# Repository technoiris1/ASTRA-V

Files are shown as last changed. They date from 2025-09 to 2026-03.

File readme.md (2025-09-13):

# ASTRA-V

heyo! Manan this side - this is my second big hardware project after my foldable 3d printer - ASTRA-V. Stands for Autonomous Stabilised Thrust Recovery Ascent Vehicle.<br>
CAD
CAD
The concept is simple - Go up - attain free fall - thrust again a lil when around 3 feet from the ground - land.

Its using LiDars to calculate the height precisely and they are pretty quick, so no problems.

First iteration -
This very iteration of ASTRA-V has the following tasks - going up 15 feet, attaining a proper stable freefall and then land. Now the word *land* is the main thing, so like this is what the hardest part is - so lets discuss the whole thing step by step.

## Launch
### Trigger
We are using a RF module to trigger the launch, it is in the flight controller.
### Process
The Servo motor will be kicked by the flight controller - which will open the flow of the O2 into the Acrylic Rod Chamber(We will come to the fuel part later on), and along with the servo - an arc ignitor will also be kicked which will burn the fuel. *sshhhhhhhhhhiiiiiiiiuuuuuuuuu* and with that the burnt fuel gases will come out pressurized of the nozzle and *shrrrooooommmm* the rockets up - it will go up 30 feet in this iteration.

## Free fall
Pretty simple, once reached the desired height(30 feet here) the valve will be kicked to close. Thus no oxidiser - thus no thrust and no more going up. Then it will just fall down - tearing down the vigilantly through the air.

## Landing
Now this is the special sauce, the complex thing - in simple words - LiDar sensors are highly sensitive sensors which mainly work on lasers so really quick. They will be sensing the altitude and sending it to the flight computer, now as soon as the altitude or around 15 feet (in this case) is reached - the computer will kick up the servo and ignitor once again to push enough thrust to neutralise the G force attained in the freefall. So like - the whole rocket will have a gentle touchdown in the air using thrusters. Now along with the engine mechanism, one more thing kicked would be the servo motors to deploy the landing legs - they have a really wide span as you can see in the images - so it gonna land really well.

## Flight Controller
Flight controller is a custom made from scratch which uses Pi pico as the main board. It uses MPU-6050 as the Gyro and BMP-280 as the altimeter as its a barometer. It has pins for breakouts of all these things along with connections with landing servos, LiDar sensors, Fuel Servos and the Arc Ignitor. It has 7 motor connections, 2 LiDar, 1 for MPU6050 and BMP280 each, it has different capacitors placed overall for fluctuations etc.
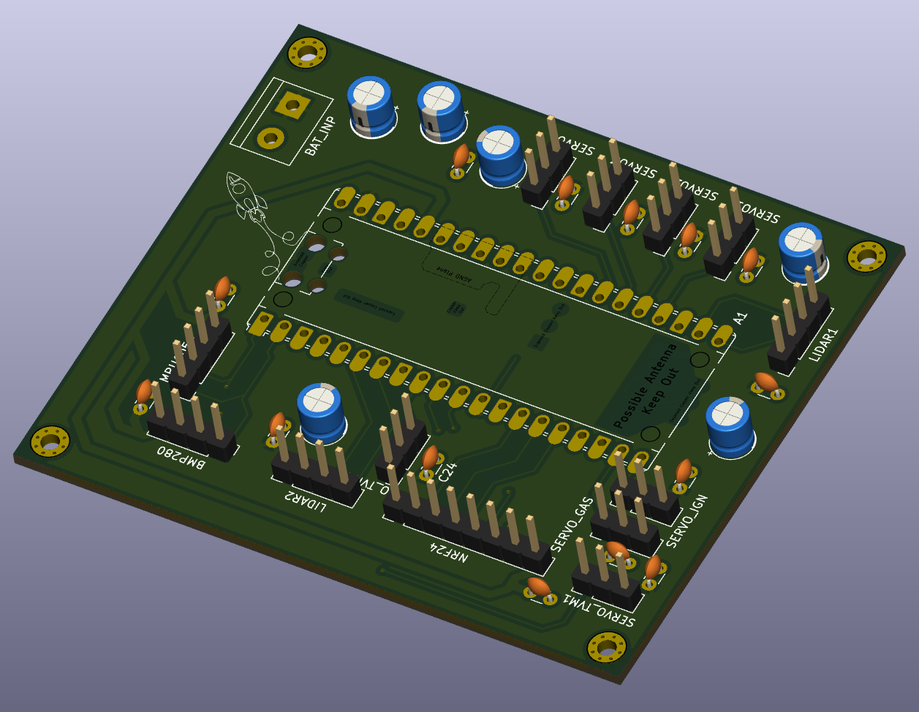
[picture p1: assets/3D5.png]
pcb


## Fuel
It is using Acrylic as a fuel along with O2 as the oxidiser. Pretty simple there is a chamber with acrylic rod and a servo controlled apparatus for the input of oxygen into the chamber. So the burnt O2 will heat up and burn the Acrylic rod, thus the Acrylic vapours will move out really really quickly off the nozzle providing thrust.

## Rocket motor and thrust vectoring
I am working on a basic servo controlled thrust vectoring system to control the direction of the thrust. This will allow for more precise control of the rocket's trajectory. The servos will be fitted on two different rings, one ring with a servo will be connected to the tube body of rocket and it will rotate another ring inside it, which is housing another servo and that servo will be connected to a ring joint to the rocket motor. So in this way there will be a whole 2-axis thrust vectoring system. I am currently working on the design and 3d model, will put here as soon as i'm done.

## Why am I making this thing?
cuz am crazy

## BOM
| ASTRA-V | 1 | 2 |  3 | 4 |  5 |  6 |
|:---|:---|:---|:---|:---|:---|:---|
| ASTRA | Autonomous Stabilised Thrust Recovery Ascent | | | | | |
| | | | | | | |
| BOM- | | | | | | |
| Name | Use case | price each | units | total price inr | total price usd | link |
| MG946R servo motors | Landing legs deployment | 800 | 4 | 3200 | 37 | https://thinkrobotics.com/products/standard-metal-servo-mg946r-1?variant=12765401514056 |
| LiDar sensor | to measure height quickly | 2500 | 2 | 5000 | 57 | https://thinkrobotics.com/products/tf-luna-lidar-tof-distance-ranging-sensor-8m |
| Raspberry pi pico W | the main controller of the flight | 700 | 2 | 1400 | 16 | https://thinkrobotics.com/products/raspberry-pi-pico-w-online?variant=44615124386109 |
| BMP280 breakout | the altimeter of the flight ctrl | 70 | 2 | 140 | 2 | https://thinkrobotics.com/products/bmp280-barometric-sensor-module-3-3v-5v?variant=32045116325974 |
| MPU 6050 | gyro sensor | 300 | 2 | 600 | 7 | https://thinkrobotics.com/products/mpu6050-gyroscope-sensor?variant=16158094786632 |
| nrf module | trigger for rocket to go boom | 80 | 2 | 160 | 2 | https://roboticsdna.in/product/nrflongrenge24l01/ |
| pin headers | pin headers on pcb | 11.5 | 20 | 250 | 3 | https://thinkrobotics.com/products/single-row-2-54-mm-pitch-header-40-pin?variant=12744266055752 |
| battery | battery | 1900 | 1 | 1900 | 22 | https://robocraze.com/products/bonka-2200mah-35c-3s1p-11-1v-lipo-battey?_pos=1&_sid=bea5fbb80&_ss=r |
| battery charger | battery charger | 350 | 1 | 350 | 4 | https://robocraze.com/products/b3-pro-li-po-battery-charger?_pos=2&_sid=bea5fbb80&_ss=r |
| 12v to 5v stepdown | as the name suggests, its the best i could find right now as i need >15A to feed to all the servos and lidars and all, gonna use a simpler one if found | 1300 | 1 | 1300 | 15 | https://www.amazon.in/Regulator-Converter-Step-Down-Waterproof-Transformer/dp/B0BB7TNNR9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 |
| 0.1uf ceramic cap | on pcb | 5 | 3 | 15 | 1 | https://quartzcomponents.com/products/10000-pf-0-1uf-ceramic-capacitor?_pos=1&_sid=c9f6e0456&_ss=r |
| 470uf cap | on pcb | 7 | 3 | 21 | 1 | https://quartzcomponents.com/products/470uf-50v-electrolytic-capacitor?_pos=1&_sid=1ae57eeec&_ss=r |
| 100uf cap | on pcb | 3 | 10 | 30 | 1 | https://quartzcomponents.com/products/100%CE%BCf-35v-radial-electrolytic-capacitor?_pos=3&_sid=f5c2847a1&_ss=r |
| 10uf cap | on pcb | 3 | 10 | 30 | 1 | https://quartzcomponents.com/products/10uf-50v-electrolytic-capacitor?_pos=2&_sid=5efdc15a5&_ss=r |
| push button | to be on the fire remote and some other usecases like replacing the arc ignitor small button with large ones to make it easier to work with | 20 | 3 | 60 | 1 | https://thinkrobotics.com/products/6mm-tactile-push-button-pack-of-20?variant=33484370313302 |
| arc igniter | lighter for the fuel etc. | 150 | 2 | 300 | 4 | https://quartzcomponents.com/products/arc-cigarette-lighter-parts-diy-electronic-lighter-kit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 |
| 18650 li-on battery | battery for the arc igniter | 100 | 2 | 200 | 3 | |
| 18650 battery charger | charger for the battery | 100 | 1 | 100 | 2 | https://quartzcomponents.com/products/18650-li-ion-battery-charger-for-single-cell?_pos=2&_sid=500a0bb39&_ss=r |
| 18650 battery holder  | holder for the battery | 25 | 1 | 25 | 1 | https://quartzcomponents.com/products/single-cell-18650-li-ion-battery-holder?_pos=1&_sid=1d517396f&_ss=r |
| flight controller PCB | main board | 5000 | 1 | 5000 | 57 | https://github.com/Manan-Coder/ASTRA-V/tree/main/Flight%20Controller |
| cardboard tube | for the main tube, it will be having the glass cloth on it | 675 | 1 | 675 | 8 | https://www.amazon.in/Inches-Mailing-Tubes-Metal-Length/dp/B0CPWVSQKS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 |
| fibre glass cloth | to make the main tube and make it durable | 650 | 1 | 650 | 8 | https://www.amazon.in/Fiber-Glass-Cloth-Thickness-10/dp/B0CX1W4TBQ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 |
| epoxy resin | to stick the glass cloth to the main tube | 500 | 1 | 500 | 6 | https://www.amazon.in/gp/product/B0F5W94NLF/ref=ewc_pr_img_1?th=1 |
| Carbon Fibre rods | Landing legs | 140 | 12 | 1680 | 20 | https://thinkrobotics.com/products/carbon-fiber-solid-tube-1-m?variant=39329659650134 |
| oxygen can | oxidiser for fuel | 1300 | 1 | 1300 | 15 | https://www.amazon.in/breathing-difficulties-Respiration-Lightweight-Travel-Friendly/dp/B0DNXRSX7V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 |
| acrylic rod | main fuel on which oxygen act as an oxidiser | 700 | 1 | 700 | 8 | https://www.amazon.in/Global-Plexiglass-Transparent-UV-Resistant-Diameter/dp/B07SR8LMRX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 |
| tube clamps | clamps for the tube carrying oxygen to the chamber | 160 | 1 | 160 | 2 | https://www.amazon.in/kitchenware-Store-clamp-pipe-safety/dp/B096NPHQLF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 |
| oxygen tube | the tube which will carry the oxygen to the chamber | 200 | 2 | 400 | 5 | https://www.amazon.in/ALEXERA-Mediplus-Oxygen-Tube-Length/dp/B0DDH3J4RS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 |
| aluminium tube | it will be the body of the rocket motor, the whole outer casing for safety and all that stuff | 1500 | 1 | 1500 | 18 | https://www.amazon.in/uxcell-Aluminum-Length-Seamless-Straight/dp/B083S6BKBW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 |
| graphite plate | it will be cnc'ed to act as the nozzle | 1300 | 1 | 1300 | 15 | https://www.amazon.in/Graphite-Operation-Practical-Craftsmanship-Thickness/dp/B0DKNLMLVY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 |
| nozzle | to make the input of oxygen clean and safe | 450 | 1 | 450 | 6 | https://www.amazon.in/Viking-Brass-Nozzle-Gas-Geysers/dp/B08GCNYLTT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 |
| aluminium plate | it will be used to make the caps of the motor, im gonna get it cnc'ed and welded by a local mechanic shop | 700 | 1 | 200 | 3 | https://www.amazon.in/Invento-Aluminium-Alloy-Sheet-300x300x2mm/dp/B074FX4M4X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 |
| | | | | | | |
| | | | | | | |
| | | | total- | 29596 | 351 | |

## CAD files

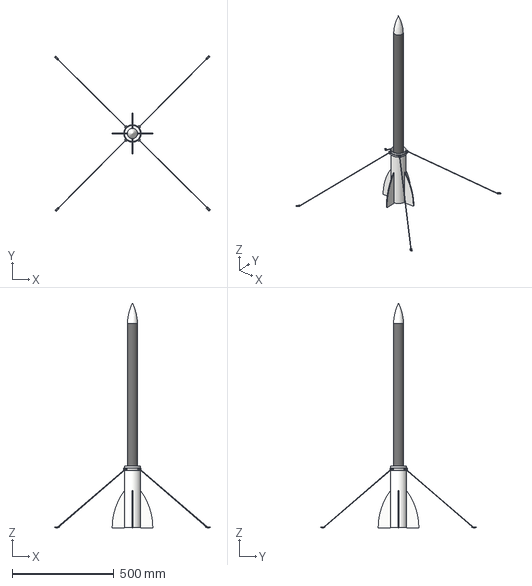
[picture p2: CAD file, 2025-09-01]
CAD/astra.step
764.9 x 765.1 x 1103.0 mm

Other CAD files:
CAD/ASTRA.stl
CAD/astra.f3d

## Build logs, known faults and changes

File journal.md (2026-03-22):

---
title: "ASTRA - Autonomous Stabilised Thrust Recovery Ascent"
author: "Manan Sharma (@Manan)"
description: "A basic paraffin powered rocket which goes up, falls down and lands on 4 legs."
created_at: "2025-07-14"
Total hours - 93 hrs
---

14th July, 2025 -
Doing research, I've been researching for about 5-6 hours now and i came to a conclusion - I am going to use hybrid oxidising motor to power my rocket as i can control them and make them work the way I want. I am locking in paraffin wax and n2o chargers for the fuel for now. I am gonna use whipped cream chargers as they suit the requirements here. Other than that I am right now studying how solenoid valves work and how can I effectively use them. Packing up for today - Its 4am.

hours - +4

---
15th July, 2025 -
Did a little more research and finalised everything - the structure and layout of everything including the positioning of the parts etc. now time to search for all the crucial hard to find parts and start with the cad model.

hours - +2

--

Started with Open Rocket - made a basic model of our rocket. Going to complete this tomorrow and simulate some test flights. signing off for today.
hour - +2.5
Open Rocket
Open Rocket
hours - +2
---

29th July, 2025 -
Need to speedrun this project in the next 3 days. ran some simulations, things look good.

Open Rocket
Open Rocket

hours - +4

---
30th and 31st July, 2025 -
Completed the cad model, with the calculations for Centre of Gravity and everything else. Decided the dimensions of the things like landing legs etc.
hours - +7

--
Also completed the research for the fuel system - the way everything will work and like the flow of the energy. Finalised the chamber design for parrafin wax and no2 chargers and all the other things. Also started working on the flight controller - researched for the parts and found the suitable things which complement each other - rn we are using - 2 lidars on either side, STM32 L052K8U6 as the MCU, MPU6050 as gyro, and BPM280 as the altimeter. Also using a RF module to make the launching system's trigger.
hours - +14

CAD
CAD

--
Completed the schematics -
CAD

hours - +5

---

August 1st and August 6th -
well while making this thing - i submitted it for an event but soon i realised that the pcb ive made is quite cooked, i should not use a stm as a first timer. so rn my goal is to remake this whole thing in the coming 3 days and ask for a rereview. lets see - these are the current things.

CAD
CAD

this pcb took around - 17 hrs

---
August 10th -
Remade some of the schematics, gonna complete all tomorrow.

SCH

hours - +4

---

August 15th -
Continued with the schematics, also had to go through a lot of things which made me go down and wanted to leave on this thing a lot of times, the thing which messed the most was the spark plug thing - the thing is that im using a 7.4V battery and a 5v buck converter to power pico and servos/lidar. But the thing is that i wasn't able to find any spark plug that could work with the 7.4V battery or the 5v buck converter thing. So i just felt like this thing isnt going anywhere as 5v or 7.4v for once is too less for something like this. So I did some more research to find if im able to find something to produce the spark working in the desired voltage, so i kinda gave up on the project as same was gonna happen with the solenoid valve, so i just slept for straight 12 hrs and woke up to do some research for the last time and surprisingly enough i found something, not a typical spark plug but a arc ignitor, i stumbled across it once before but kinda didn't look at it because it just felt too unreliable and I had spark plugs in my mind. So yeah i thought that i'd just use an arc ignitor with a power from pcb power rail and like control using gpio from pico using logic shifters or something if needed but then i realise that the only arc ignitor available here is a breakout with a button to put it up fire, so its like a plasma thing between two closely placed naked wires, so depression came in again, but then i realised that i am getting a bambu a1 mini real soon from shipwrecked so i just decided that i'd make a gear system with a servo motor controlled by the flight controller to press the button to put it up and roll back when it is not supposed to be pressed, so yeah thats it. Now i gotta figure out to use solenoid valves with the voltage limitation as im only finding 24v valves which can actually control the gas etc. and then gotta finalise the fuel system.

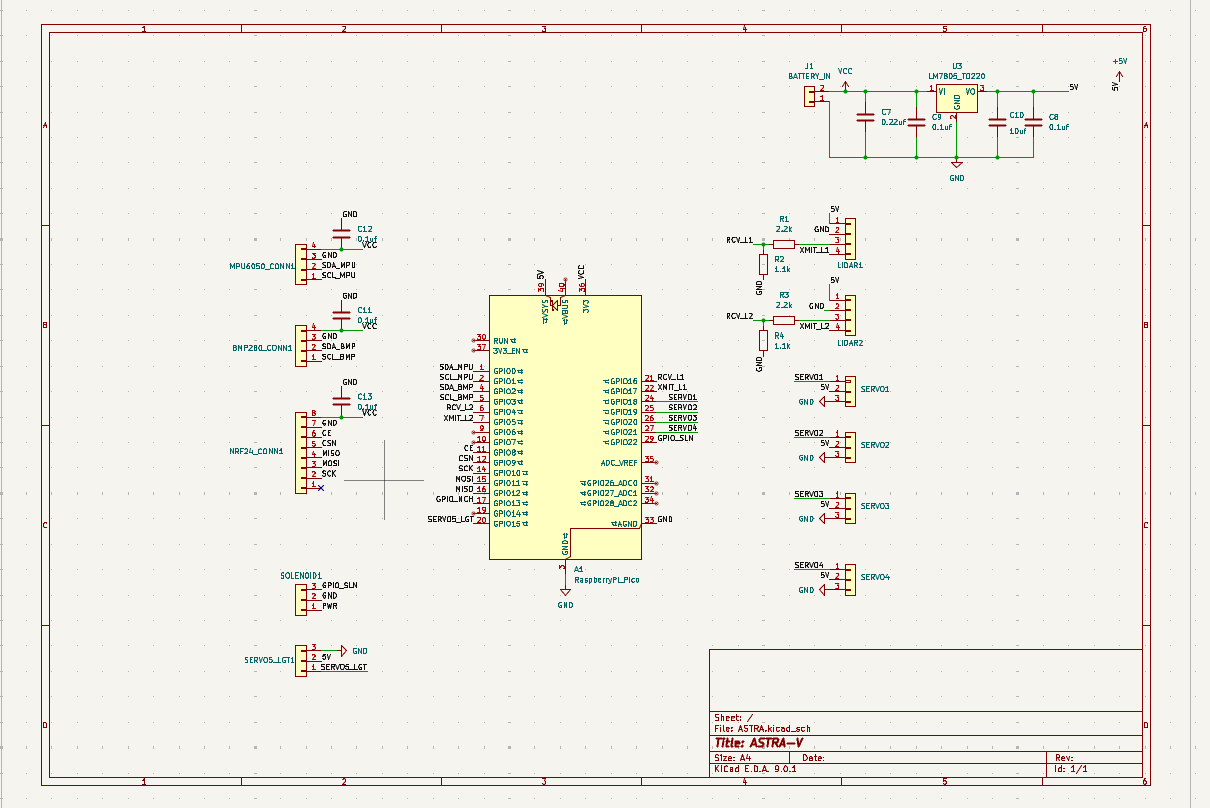
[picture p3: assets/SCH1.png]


hours - +7

---
August 19th -
ok so the thing is that we are on the verge of completing the pcb, i just routed everything and completed everything - might add some capacitors and decoupling caps for safety other than that the core thing is done. i decided to go with just gaseous fuel for now than a oxidiser and fuel thing - so we are using butane and not gonna use solenoid valves, we just gonna use canisters with a 3d printed apparatus which will push and spray the gas into a chamber via tube when servo motor pulls it, and the servo will be controlled with the flight contoller, yep so did research - routed everything and compiled the BOM. Just finishing touches left.

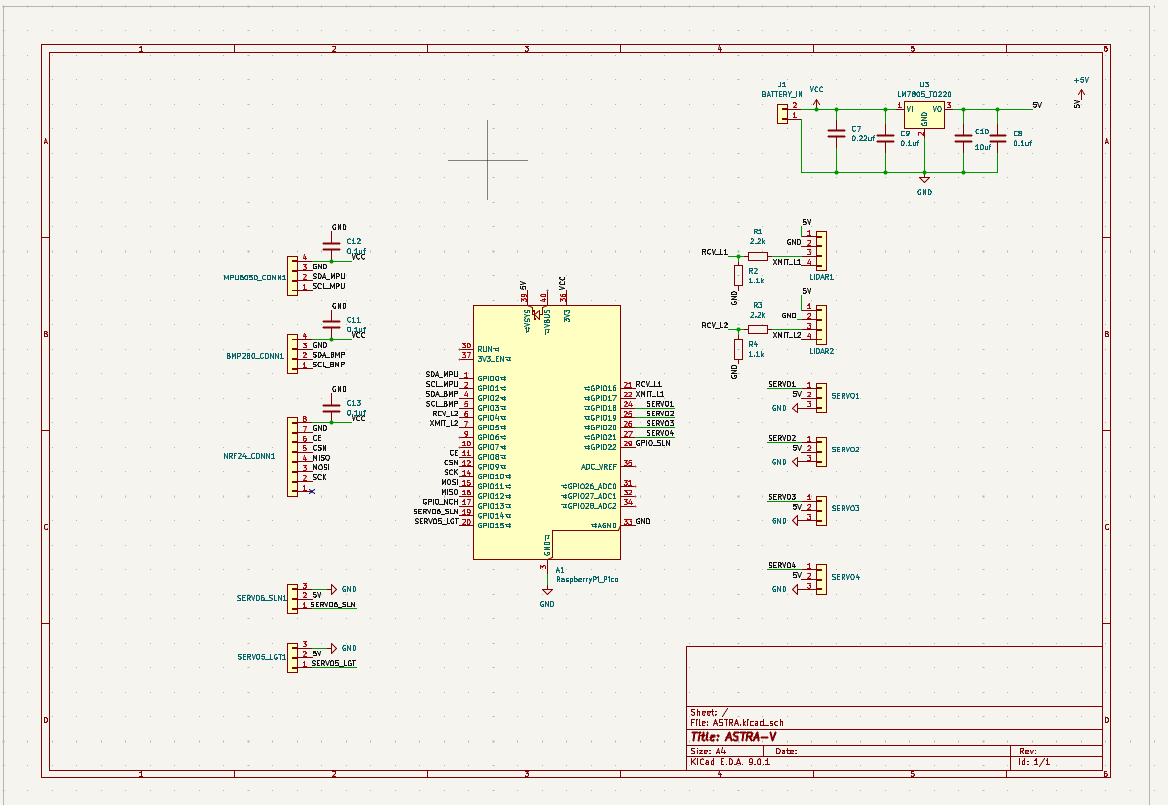
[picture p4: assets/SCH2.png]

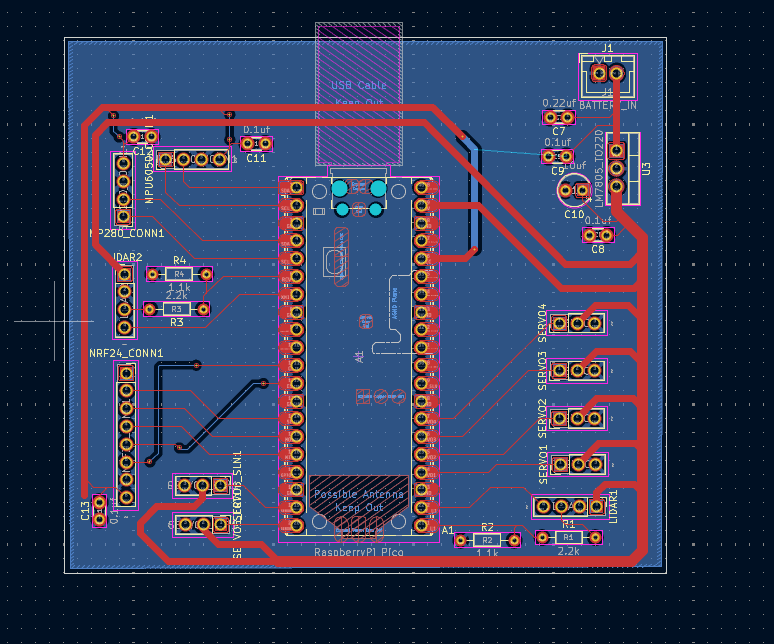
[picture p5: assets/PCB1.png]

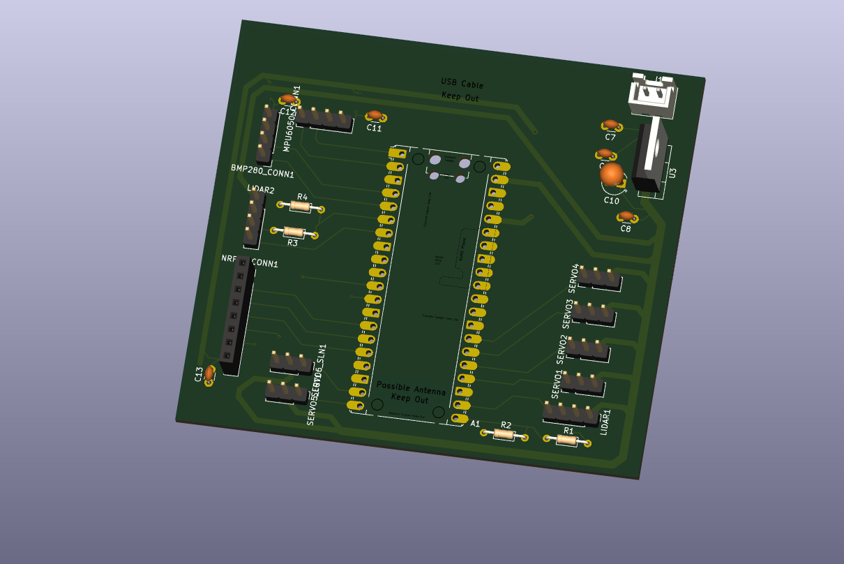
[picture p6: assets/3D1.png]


hours - +11

---
August 20th -
hmmm SOOO the pcb is done, complete! yup so i made a system on what im gonna do with the fuel system as solenoid is something that cant be used with this pcb like this, so we made a setup to use a butane can and use a servo to press and release gas into a combustion chamber through a tube, and the servo will be controlled with the flight controller. yup so other thing is that i changed the thick 5v traces with a 5v plane finally, so we have two planes one for ground. So yeah PCB is done, added all the capacitors for all the components - 0.1uf ceramic at every component, 100uf electrolytic at every cluster of power consuming comps like servos and lidar, and 470uf electrolytic and a 10uf at the same place. We are using a 11.1v battery and a stepdown converter converting it to 5V which is powering the pico, servos and LiDar, and the 3v3 pin of the pico is powering MPU6050, BMP280 and the nrf module. Also added a few sketches and texts on the silkscreen - one is a rocket sketch i found online, one is GSLV - an indegenious launch vehicle developed by ISRO and a sketch of Neil Armstrong on the moon.
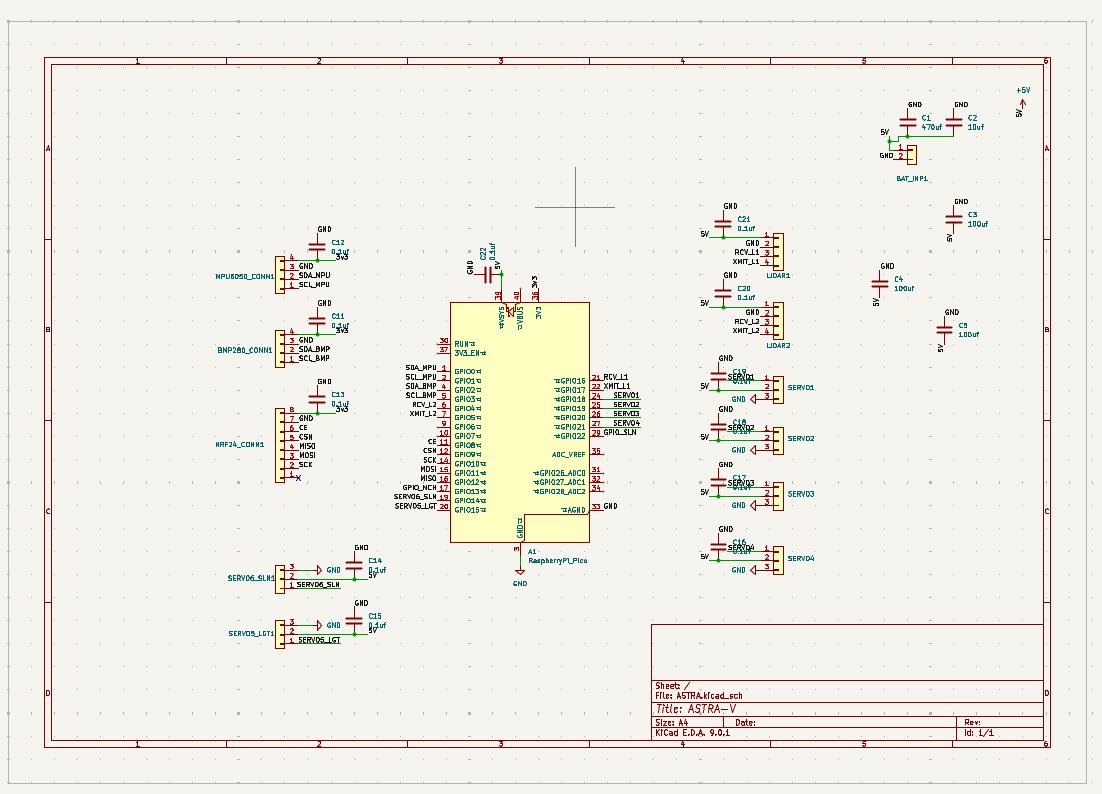
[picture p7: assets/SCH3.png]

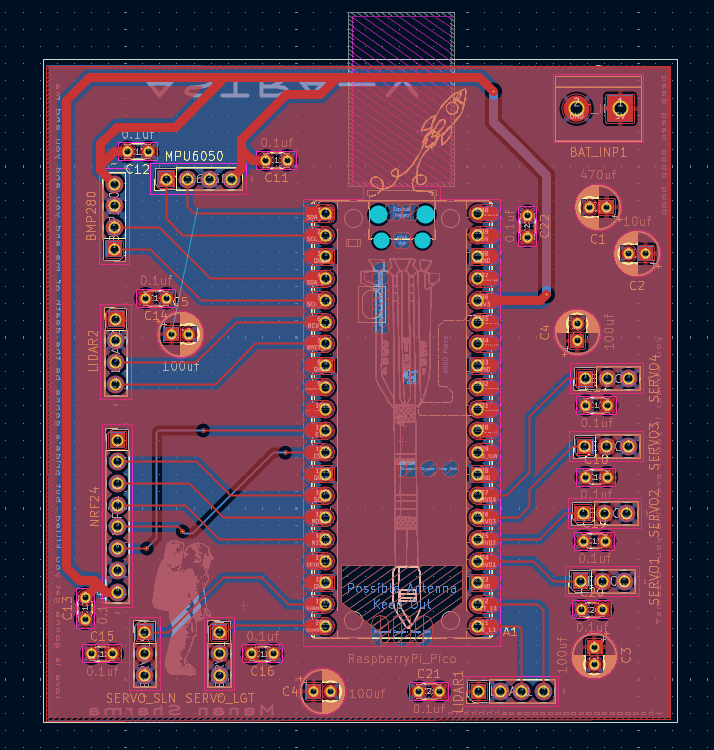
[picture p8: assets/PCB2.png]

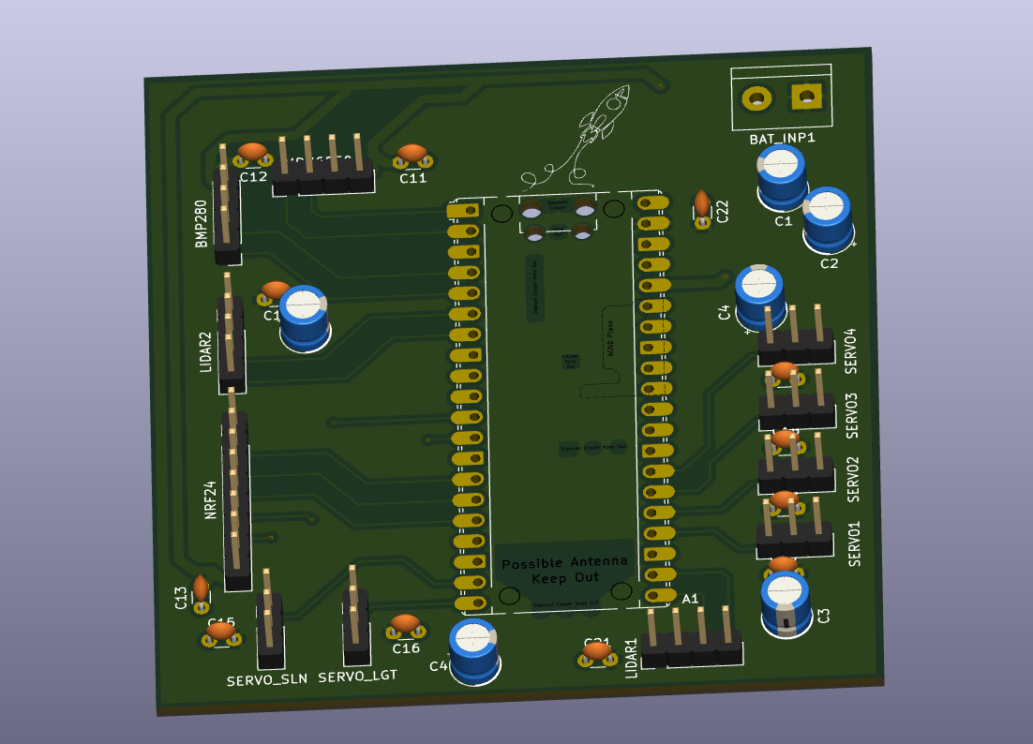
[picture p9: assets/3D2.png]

SCH

hours - +6

---
September 13th -
So yeah a big break, i was done with the initial design everything, then a while ago i felt like making a thrust vectoring system to ensure that it stays straight as I was 100% of it getting tilted, so yeah other than that - i also optimised the flight controller pcb by a lot, I am done with the pcb now and below are the images, also yeah I got a 370$ grant to build this thing irl, so yeah im going to finalise everything tomorrow and then start ordering stuff.
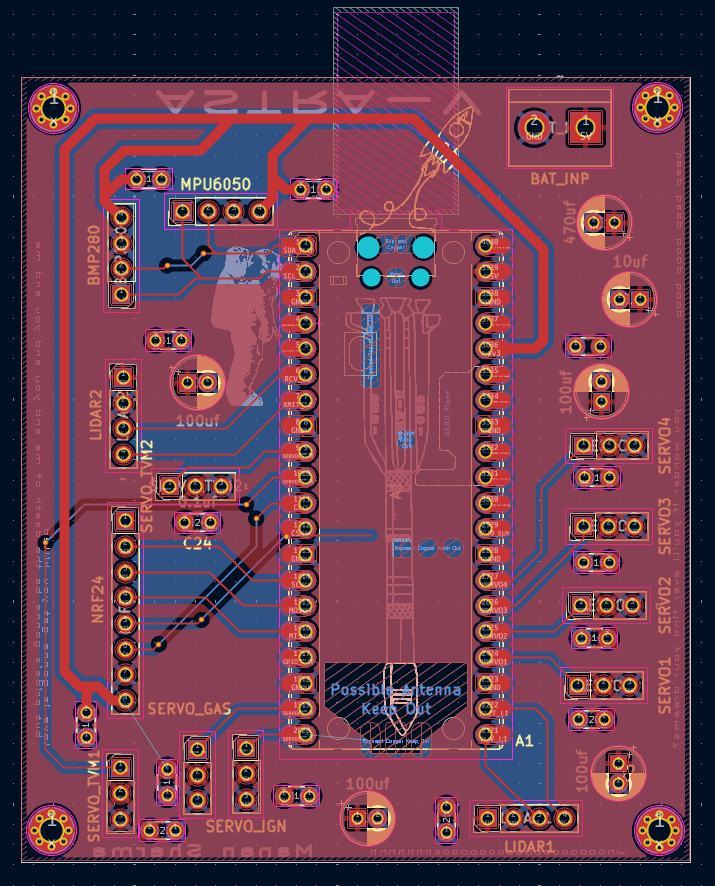
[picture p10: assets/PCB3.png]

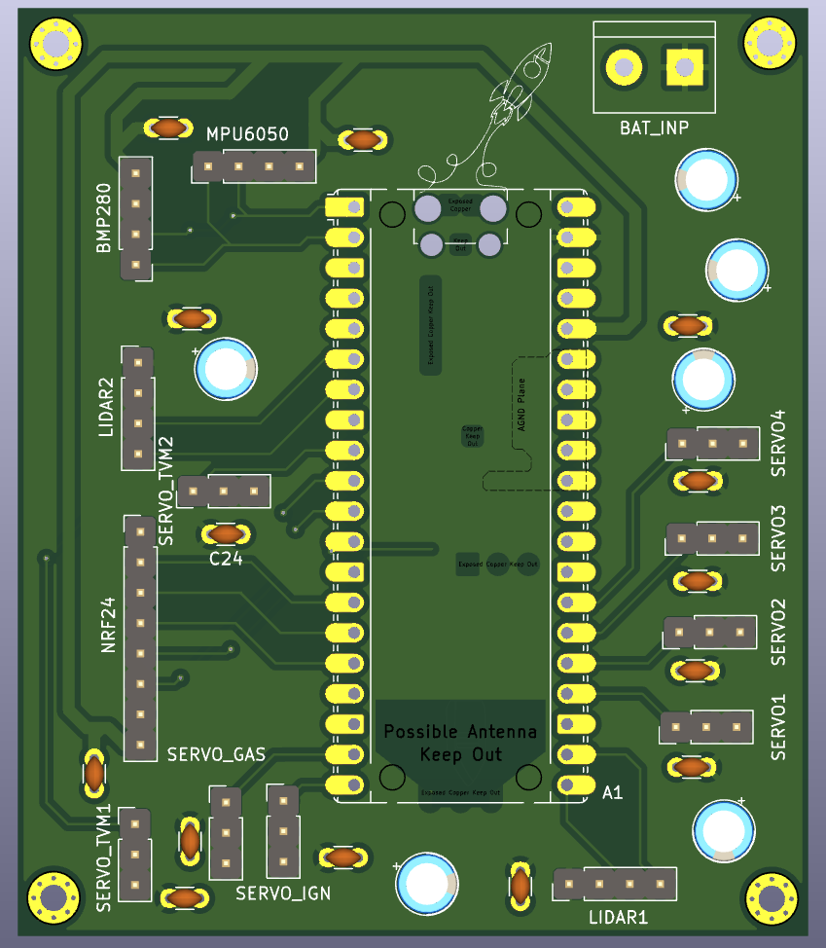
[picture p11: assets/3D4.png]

PCB
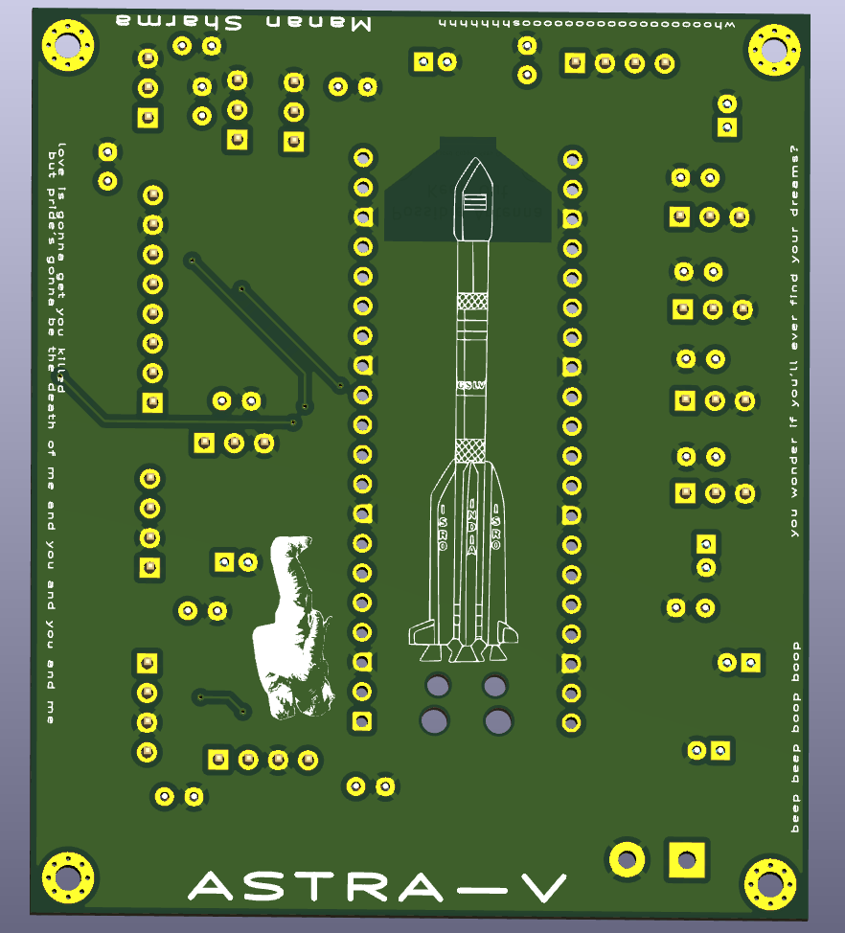
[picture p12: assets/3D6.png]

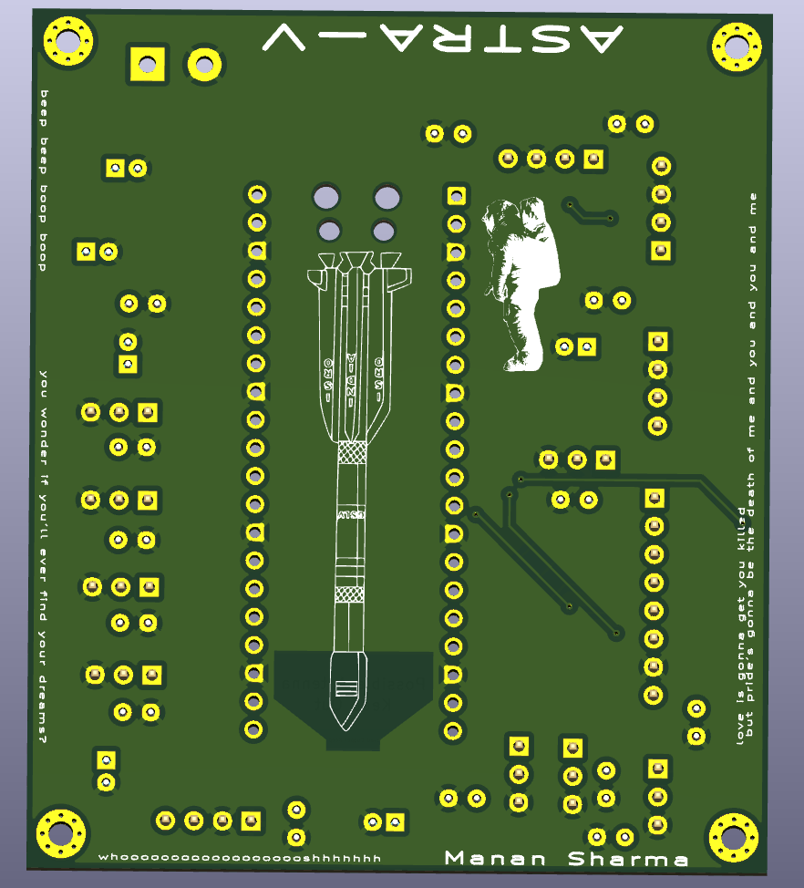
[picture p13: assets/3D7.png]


hours - +10

---
Build Journal -

## entry 1
got the PCB of the flight controller and soldered all the parts on it. i just soldered pin headers to connect the raspberry pi pico and other pin headers for different motors on it.
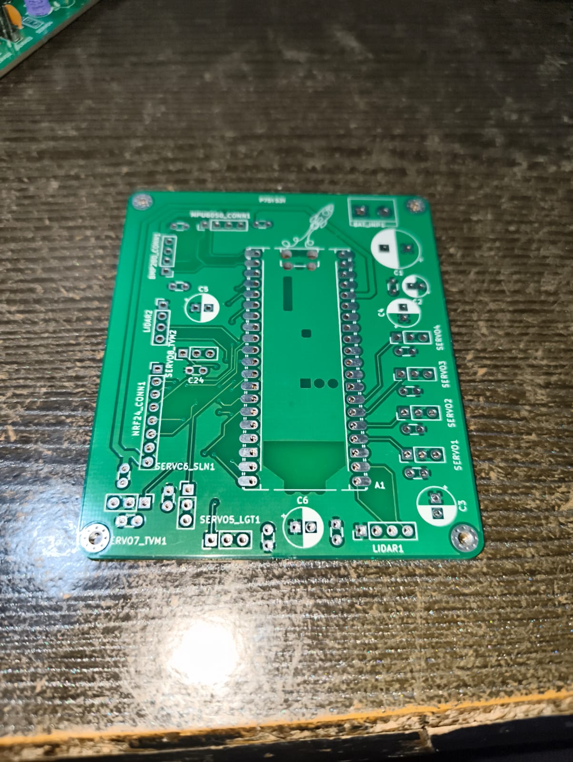
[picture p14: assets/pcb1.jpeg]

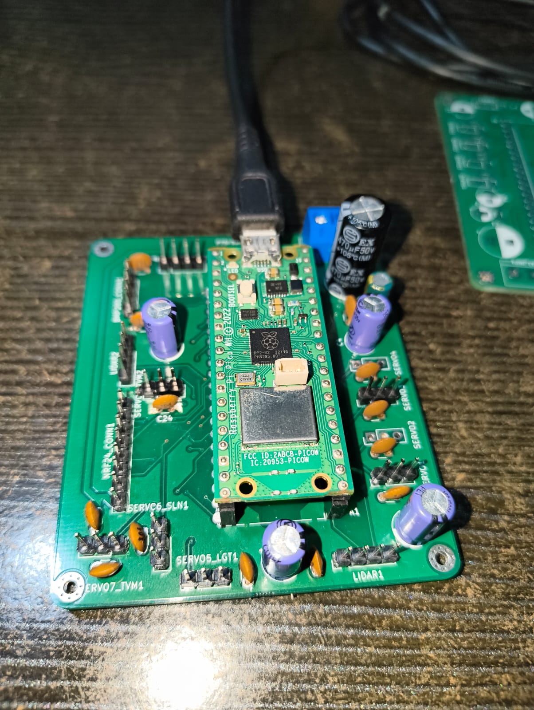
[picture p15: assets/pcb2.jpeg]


## entry 2
yo! there hasnt been any update on this project for a pretty long time, the main reason is that I'm too swamped with other things and I need to completely redesigng the whole mechanism. So far I was trying to make a rocket motor at home all by myself but thats not something which one should be doing in their bedroom, its extremely dangerous and can wipe me out of existence if i mess up, so i talked in a few online rocketry communities and every advice i received was that you should start with basic solid fuel, which is true. But the issue is that you can't achieve a controlled flow with solid propellant, it will blow off and only stop when it's over. So I came up with a new thing, what if we just use solid propellant to push the rocket up and throw it in the air and then use brushless motors with propellers to make it land, so like just 4 hands pop out with motors at the time of landing and help it land smoothly, this is a lot of achievable thing than what i was working, this project is something i really wanna see happen and land properly, im setting a goal of 1st august to complete it and make it land rn. Today is 22nd March, so I have a little over 4 months. cya o7

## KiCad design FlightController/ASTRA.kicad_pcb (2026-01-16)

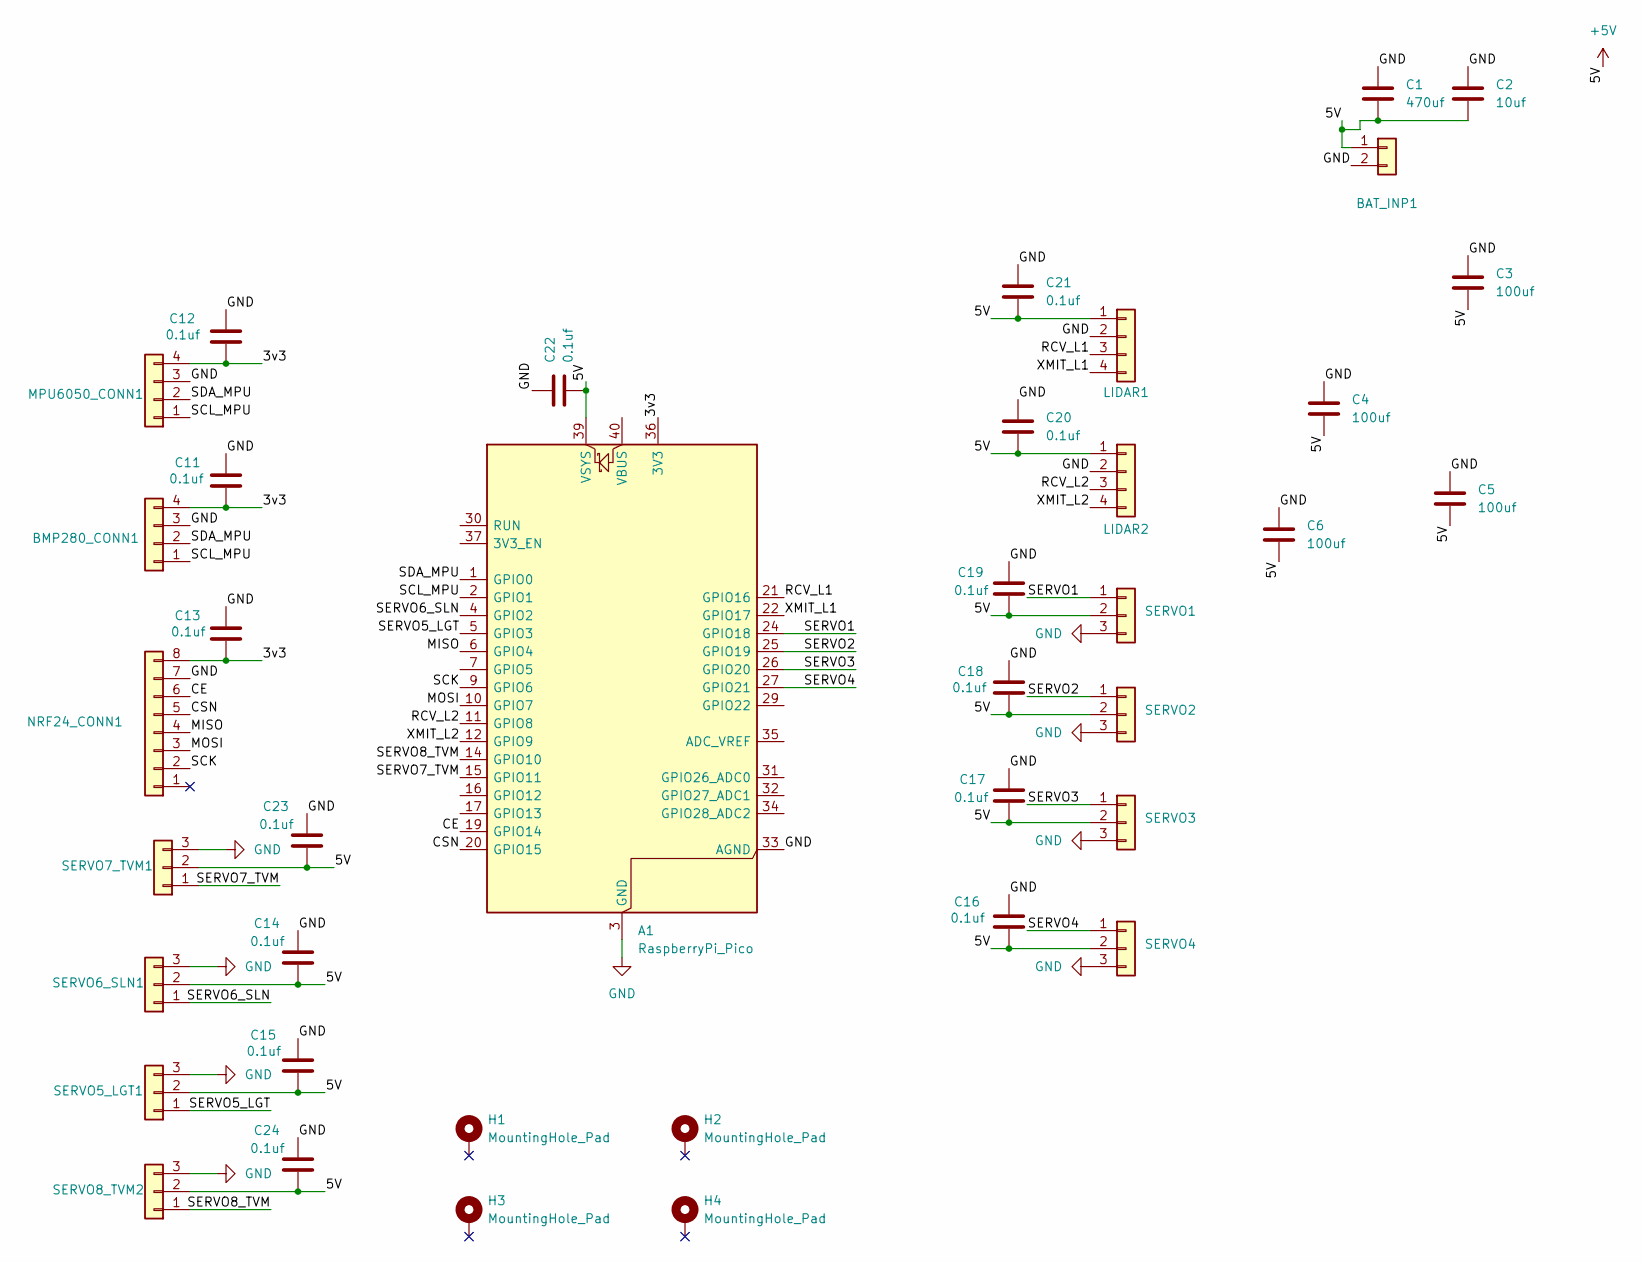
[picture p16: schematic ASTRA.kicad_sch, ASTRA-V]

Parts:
A1: RaspberryPi_Pico; RaspberryPi_Pico_Common_Unspecified
BAT_INP1: TerminalBlock_bornier-2_P5.08mm
BMP280_CONN1: PinHeader_1x04_P2.54mm_Vertical
C1: 470uf; CP_Radial_D10.0mm_P5.00mm
C2: 10uf; CP_Radial_D5.0mm_P2.00mm
C3, C4, C5, C6: 100uf; CP_Radial_D6.3mm_P2.50mm
C11, C12, C13, C14, C15, C16, C17, C18, C19, C20, C21, C22, C23, C24: 0.1uf; C_Disc_D3.0mm_W1.6mm_P2.50mm
H1, H2, H3, H4: MountingHole_Pad; MountingHole_2.2mm_M2_Pad_Via
LIDAR1, LIDAR2: PinHeader_1x04_P2.54mm_Vertical
MPU6050_CONN1: PinHeader_1x04_P2.54mm_Vertical
NRF24_CONN1: PinHeader_1x08_P2.54mm_Vertical
SERVO1, SERVO2, SERVO3, SERVO4, SERVO5_LGT1, SERVO6_SLN1, SERVO7_TVM1, SERVO8_TVM2: PinHeader_1x03_P2.54mm_Vertical

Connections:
/3v3: A1.36 (3V3), BMP280_CONN1.4, C11.2, C12.2, C13.2, MPU6050_CONN1.4, NRF24_CONN1.8
/5V: A1.39 (VSYS), BAT_INP1.1, C1.1, C2.1, C3.1, C4.1, C5.1, C6.1, C14.2, C15.2, C16.2, C17.2, C18.2, C19.2, C20.2, C21.2, C22.2, C23.2, C24.2, LIDAR1.1, LIDAR2.1, SERVO1.2, SERVO2.2, SERVO3.2, SERVO4.2, SERVO5_LGT1.2, SERVO6_SLN1.2, SERVO7_TVM1.2, SERVO8_TVM2.2
/CE: A1.19 (GPIO14), NRF24_CONN1.6
/CSN: A1.20 (GPIO15), NRF24_CONN1.5
/MISO: A1.6 (GPIO4), NRF24_CONN1.4
/MOSI: A1.10 (GPIO7), NRF24_CONN1.3
/RCV_L1: A1.21 (GPIO16), LIDAR1.3
/RCV_L2: A1.11 (GPIO8), LIDAR2.3
/SCK: A1.9 (GPIO6), NRF24_CONN1.2
/SCL_MPU: A1.2 (GPIO1), BMP280_CONN1.1, MPU6050_CONN1.1
/SDA_MPU: A1.1 (GPIO0), BMP280_CONN1.2, MPU6050_CONN1.2
/SERVO1: A1.24 (GPIO18), SERVO1.1
/SERVO2: A1.25 (GPIO19), SERVO2.1
/SERVO3: A1.26 (GPIO20), SERVO3.1
/SERVO4: A1.27 (GPIO21), SERVO4.1
/SERVO5_LGT: A1.5 (GPIO3), SERVO5_LGT1.1
/SERVO6_SLN: A1.4 (GPIO2), SERVO6_SLN1.1
/SERVO7_TVM: A1.15 (GPIO11), SERVO7_TVM1.1
/SERVO8_TVM: A1.14 (GPIO10), SERVO8_TVM2.1
/XMIT_L1: A1.22 (GPIO17), LIDAR1.4
/XMIT_L2: A1.12 (GPIO9), LIDAR2.4
GND: A1.3 (GND), A1.8 (GND), A1.13 (GND), A1.18 (GND), A1.23 (GND), A1.28 (GND), A1.33 (AGND), A1.38 (GND), BAT_INP1.2, BMP280_CONN1.3, C1.2, C2.2, C3.2, C4.2, C5.2, C6.2, C11.1, C12.1, C13.1, C14.1, C15.1, C16.1, C17.1, C18.1, C19.1, C20.1, C21.1, C22.1, C23.1, C24.1, LIDAR1.2, LIDAR2.2, MPU6050_CONN1.3, NRF24_CONN1.7, SERVO1.3, SERVO2.3, SERVO3.3, SERVO4.3, SERVO5_LGT1.3, SERVO6_SLN1.3, SERVO7_TVM1.3, SERVO8_TVM2.3

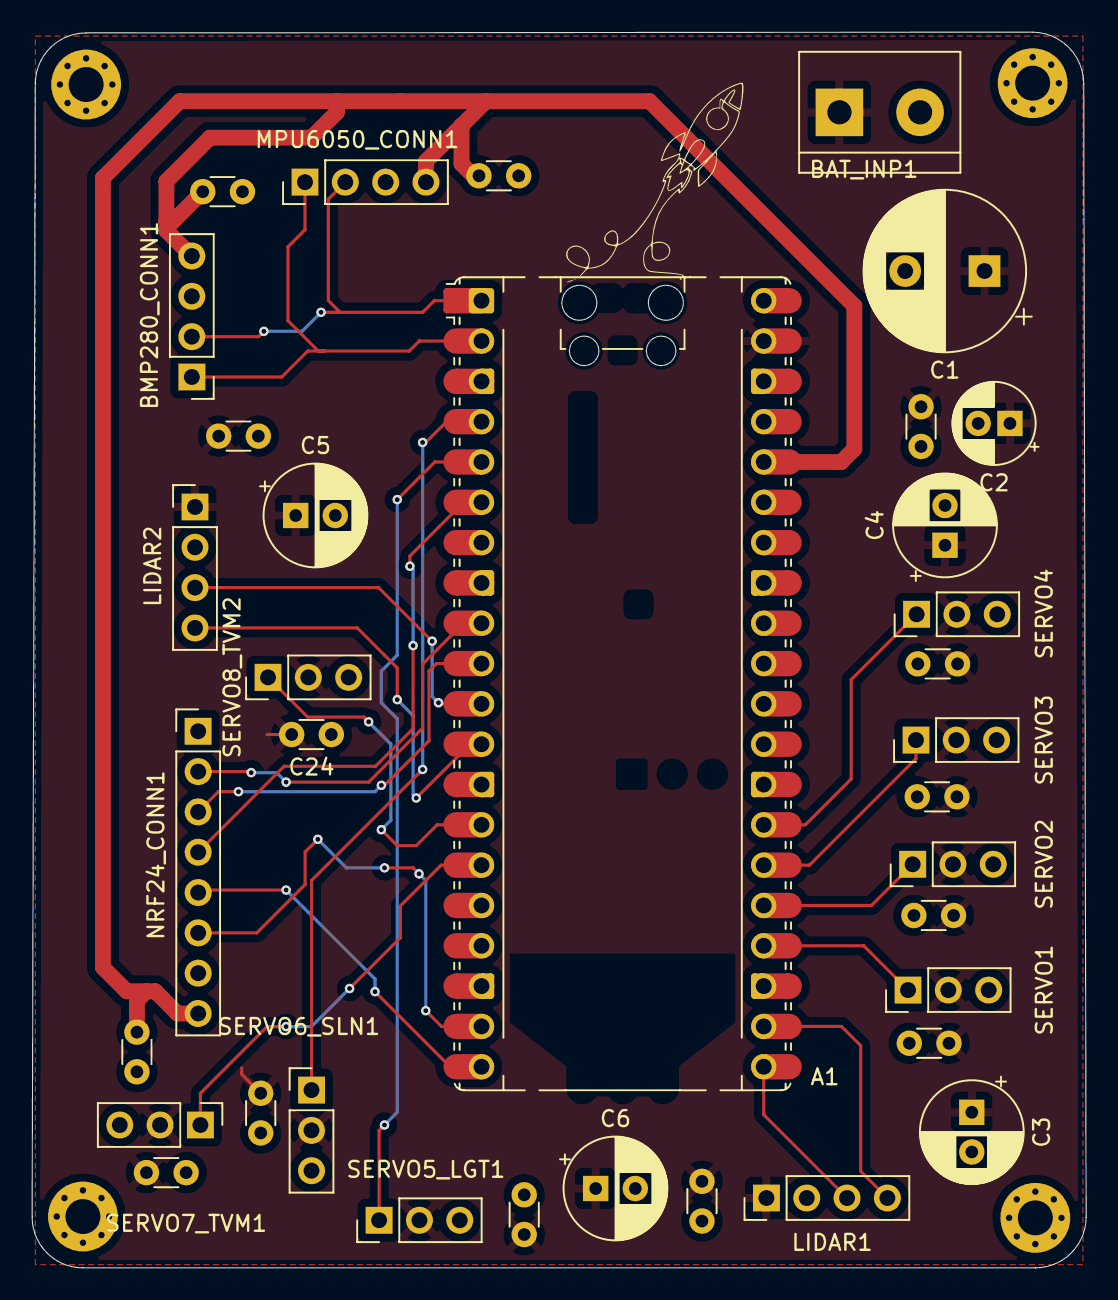
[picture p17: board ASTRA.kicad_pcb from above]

Board: 2 copper layers, 66.4 x 77.8 mm, 39 parts (0 on the bottom side), 22 nets.

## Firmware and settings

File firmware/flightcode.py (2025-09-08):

'''
ASTRA-V flight code
this is most probably not going to be used in its current form as once i get im going to do a lot of testing
and things are going to change a lot over iterations but this is my interpretation of what its base would look like

note - AI was used in creation of this code as this is something not going to be used to fire the rocket.
'''
from machine import Pin, I2C, UART, PWM
import time
import uos

PLACEHOLDER_FUEL_SERVO_PIN = 14
PLACEHOLDER_IGNITER_SERVO_PIN = 15
PLACEHOLDER_LEG_SERVO_PINS = [18,19,20,21]

PLACEHOLDER_I2C_SDA = 0
PLACEHOLDER_I2C_SCL = 1

PLACEHOLDER_TFLUNA_UART0_TX = 0
PLACEHOLDER_TFLUNA_UART0_RX = 1
PLACEHOLDER_TFLUNA_UART1_TX = 4
PLACEHOLDER_TFLUNA_UART1_RX = 5

PLACEHOLDER_TRIGGER_PIN = 6

PLACEHOLDER_ARM_SWITCH_PIN = 7

PLACEHOLDER_IGNITER_POWER_PIN = 10

TF_LUNA_BAUD = 115200

SERVO_FREQ = 50

SERVO_MIN_US = 500
SERVO_MAX_US = 2500

APOGEE_SHUTOFF_FT = 15.0
APOGEE_SHUTOFF_M = APogee_cut = APOL = APOGEE_SHUTOFF_FT * 0.3048

REAPPLY_ALT_LOW_FT = 4.5
REAPPLY_ALT_HIGH_FT = 5.0
REAPPLY_ALT_LOW_M = REAPPLY_ALT_LOW_FT * 0.3048
REAPPLY_ALT_HIGH_M = REAPPLY_ALT_HIGH_FT * 0.3048

VALVE_OPEN_MS = 250
IGNITE_PULSE_MS = 200
ARM_HOLD_MS = 2000
SAFETY_TIMEOUT_MS = 20000

LOG_FILENAME = "log.csv"

def pwm_us_to_duty(us):

    period_us = 1_000_000 // SERVO_FREQ
    duty = int((us / period_us) * 65535)
    if duty < 0: duty = 0
    if duty > 65535: duty = 65535
    return duty

class Servo:
    def __init__(self, pwm_pin):
        self.pwm = PWM(Pin(pwm_pin))
        self.pwm.freq(SERVO_FREQ)
        self.min_us = SERVO_MIN_US
        self.max_us = SERVO_MAX_US

    def set_us(self, us):
        duty = pwm_us_to_duty(us)
        self.pwm.duty_u16(duty)

    def set_angle(self, angle):

        us = self.min_us + (self.max_us - self.min_us) * (angle/180.0)
        self.set_us(int(us))

    def detach(self):
        self.pwm.deinit()

i2c = I2C(0, scl=Pin(PLACEHOLDER_I2C_SCL), sda=Pin(PLACEHOLDER_I2C_SDA), freq=400000)

MPU_ADDR = 0x68
def init_mpu6050():
    try:
        i2c.writeto_mem(MPU_ADDR, 0x6B, b'\x00')

        print("MPU6050 init OK")
    except Exception as e:
        print("MPU6050 init failed:", e)

def read_mpu6050():

    try:
        data = i2c.readfrom_mem(MPU_ADDR, 0x3B, 14)
        ax = int.from_bytes(data[0:2], 'big', signed=True) / 16384.0
        ay = int.from_bytes(data[2:4], 'big', signed=True) / 16384.0
        az = int.from_bytes(data[4:6], 'big', signed=True) / 16384.0
        gx = int.from_bytes(data[8:10], 'big', signed=True) / 131.0
        gy = int.from_bytes(data[10:12], 'big', signed=True) / 131.0
        gz = int.from_bytes(data[12:14], 'big', signed=True) / 131.0
        return (ax, ay, az, gx, gy, gz)
    except Exception as e:

        return (None, None, None, None, None, None)

BMP_ADDR = 0x76

def init_bmp280():
    try:

        i2c.writeto_mem(BMP_ADDR, 0xE0, b'\xB6')
        time.sleep_ms(2)

        i2c.writeto_mem(BMP_ADDR, 0xF4, b'\x27')
        i2c.writeto_mem(BMP_ADDR, 0xF5, b'\xA0')

        calib = i2c.readfrom_mem(BMP_ADDR, 0x88, 24)

        global dig_T1, dig_T2, dig_T3, dig_P1, dig_P2, dig_P3, dig_P4, dig_P5, dig_P6, dig_P7, dig_P8, dig_P9
        dig_T1 = int.from_bytes(calib[0:2], 'little')
        dig_T2 = int.from_bytes(calib[2:4], 'little', signed=True)
        dig_T3 = int.from_bytes(calib[4:6], 'little', signed=True)
        dig_P1 = int.from_bytes(calib[6:8], 'little')
        dig_P2 = int.from_bytes(calib[8:10], 'little', signed=True)
        dig_P3 = int.from_bytes(calib[10:12], 'little', signed=True)
        dig_P4 = int.from_bytes(calib[12:14], 'little', signed=True)
        dig_P5 = int.from_bytes(calib[14:16], 'little', signed=True)
        dig_P6 = int.from_bytes(calib[16:18], 'little', signed=True)
        dig_P7 = int.from_bytes(calib[18:20], 'little', signed=True)
        dig_P8 = int.from_bytes(calib[20:22], 'little', signed=True)
        dig_P9 = int.from_bytes(calib[22:24], 'little', signed=True)
        print("BMP280 init OK")
    except Exception as e:
        print("BMP280 init failed:", e)

t_fine = 0
def read_bmp280():

    global t_fine
    try:
        data = i2c.readfrom_mem(BMP_ADDR, 0xF7, 6)
        pres_raw = (data[0]<<12) | (data[1]<<4) | (data[2]>>4)
        temp_raw = (data[3]<<12) | (data[4]<<4) | (data[5]>>4)

        var1 = (((temp_raw>>3) - (dig_T1<<1)) * dig_T2) >> 11
        var2 = (((((temp_raw>>4) - dig_T1) * ((temp_raw>>4) - dig_T1)) >> 12) * dig_T3) >> 14
        t_fine = var1 + var2
        temp_c = ((t_fine * 5) + 128) >> 8
        temp_c = temp_c / 100.0

        var1_p = t_fine - 128000
        var2_p = var1_p * var1_p * dig_P6
        var2_p = var2_p + ((var1_p * dig_P5) << 17)
        var2_p = var2_p + (dig_P4 << 35)
        var1_p = ((var1_p * var1_p * dig_P3) >> 8) + ((var1_p * dig_P2) << 12)
        var1_p = (((1 << 47) + var1_p) * dig_P1) >> 33
        if var1_p == 0:
            return (temp_c, None)
        p = 1048576 - pres_raw
        p = int((((p << 31) - var2_p) * 3125) / var1_p)
        var1_p = (dig_P9 * (p >> 13) * (p >> 13)) >> 25
        var2_p = (dig_P8 * p) >> 19
        p = ((p + var1_p + var2_p) >> 8) + (dig_P7 << 4)
        pressure = p / 256.0
        return (temp_c, pressure)
    except Exception as e:

        return (None, None)

class TFLuna:
    def __init__(self, uart_id, rx_pin, tx_pin=None):

        self.uart = UART(uart_id, baudrate=TF_LUNA_BAUD, rx=Pin(rx_pin), tx=Pin(tx_pin) if tx_pin is not None else None)

        while self.uart.any():
            self.uart.read()

    def read_distance(self):

        if self.uart.any() < 9:
            return None
        data = self.uart.read(9)

        idx = data.find(b'\x59\x59')
        if idx == -1:

            self.uart.read(1)
            return None
        if idx + 9 > len(data):
            return None
        frame = data[idx:idx+9]

        dist = frame[2] + (frame[3] << 8)
        strength = frame[4] + (frame[5] << 8)
        temp = frame[6] + frame[7] / 100.0

        return dist / 100.0

fuel_servo = Servo(PLACEHOLDER_FUEL_SERVO_PIN)
igniter_servo = Servo(PLACEHOLDER_IGNITER_SERVO_PIN)
leg_servos = [Servo(p) for p in PLACEHOLDER_LEG_SERVO_PINS]
other_servos = [Servo(p) for p in PLACEHOLDER_OTHER_SERVO_PINS]

igniter_power = Pin(PLACEHOLDER_IGNITER_POWER_PIN, Pin.OUT)
igniter_power.value(0)

trigger_pin = Pin(PLACEHOLDER_TRIGGER_PIN, Pin.IN, Pin.PULL_DOWN)
arm_switch = Pin(PLACEHOLDER_ARM_SWITCH_PIN, Pin.IN, Pin.PULL_DOWN)

tfluna0 = TFLuna(0, PLACEHOLDER_TFLUNA_UART0_RX, PLACEHOLDER_TFLUNA_UART0_TX)
tfluna1 = TFLuna(1, PLACEHOLDER_TFLUNA_UART1_RX, PLACEHOLDER_TFLUNA_UART1_TX)

init_mpu6050()
init_bmp280()

def log_init():

    try:
        if LOG_FILENAME not in uos.listdir():
            with open(LOG_FILENAME, "w") as f:
                f.write("t_ms, state, ax,ay,az,gx,gy,gz, tempC, pressurePa, dist0_m, dist1_m\n")
    except Exception as e:
        print("Log init error:", e)

def log_row(state, ax,ay,az,gx,gy,gz, tempC, pressure, d0, d1):
    t_ms = time.ticks_ms()
    try:
        with open(LOG_FILENAME, "a") as f:
            f.write("{},{},{},{},{},{},{},{},{},{},{}\n".format(
                t_ms, state,
                ax if ax is not None else "",
                ay if ay is not None else "",
                az if az is not None else "",
                gx if gx is not None else "",
                gy if gy is not None else "",
                gz if gz is not None else "",
                tempC if tempC is not None else "",
                pressure if pressure is not None else "",
                d0 if d0 is not None else "",
                d1 if d1 is not None else ""
            ))
    except Exception as e:
        print("Log write err", e)

def servo_open_fuel():

    fuel_servo.set_angle(120)

def servo_close_fuel():
    fuel_servo.set_angle(10)

def servo_ignite_press():

    igniter_servo.set_angle(120)

def servo_ignite_release():
    igniter_servo.set_angle(10)

def deploy_legs():
    for s in leg_servos:
        s.set_angle(90)
        time.sleep_ms(100)

    time.sleep(1)
    for s in leg_servos:
        s.detach()

def wait_for_arm():
    print("Waiting for ARM switch ON and hold {} ms...".format(ARM_HOLD_MS))
    while True:
        if arm_switch.value():
            t0 = time.ticks_ms()
            while arm_switch.value():
                if time.ticks_diff(time.ticks_ms(), t0) >= ARM_HOLD_MS:
                    print("ARM confirmed")
                    return True
                time.sleep_ms(10)
        time.sleep_ms(50)

def wait_for_trigger(timeout_ms=None):
    print("Waiting for trigger signal (nRF) or manual input...")
    start = time.ticks_ms()
    while True:
        if trigger_pin.value():
            print("Trigger received")
            return True
        if timeout_ms is not None and time.ticks_diff(time.ticks_ms(), start) > timeout_ms:
            print("Trigger wait timeout")
            return False
        time.sleep_ms(20)

def fire_sequence_once():

    t_start = time.ticks_ms()
    servo_open_fuel()
    time.sleep_ms(30)

    try:
        igniter_power.value(1)
    except:
        pass
    servo_ignite_press()
    time.sleep_ms(IGNITE_PULSE_MS)
    servo_ignite_release()
    try:
        igniter_power.value(0)
    except:
        pass

    time.sleep_ms(VALVE_OPEN_MS - IGNITE_PULSE_MS if VALVE_OPEN_MS>IGNITE_PULSE_MS else 50)
    servo_close_fuel()
    return time.ticks_diff(time.ticks_ms(), t_start)

def read_lidars():
    d0 = tfluna0.read_distance()
    d1 = tfluna1.read_distance()
    return d0, d1

def mission_main_loop():
    log_init()
    print("Entering mission control loop.")

    if not wait_for_arm():
        print("Not armed.")
        return

    if not wait_for_trigger(timeout_ms=60000):
        print("No trigger - abort.")
        return

    print("Trigger accepted - starting initial burn")
    state = "initial_burn"
    burn_start = time.ticks_ms()

    servo_open_fuel()

    time.sleep_ms(40)
    try:
        igniter_power.value(1)
    except:
        pass
    servo_ignite_press()
    time.sleep_ms(IGNITE_PULSE_MS)
    servo_ignite_release()
    try:
        igniter_power.value(0)
    except:
        pass

    apogee_reached = False
    shutoff_time = None
    while True:

        ax,ay,az,gx,gy,gz = read_mpu6050()
        tempC, pressure = read_bmp280()
        d0, d1 = read_lidars()

        alt_m = None
        if d0 is not None and d1 is not None:
            alt_m = min(d0,d1)
        elif d0 is not None:
            alt_m = d0
        elif d1 is not None:
            alt_m = d1

        log_row(state, ax,ay,az,gx,gy,gz, tempC, pressure, d0, d1)

        if alt_m is not None and alt_m >= APogee_cut:
            print("Apogee threshold reached (alt_m={:.2f} m) - shutting off fuel".format(alt_m))
            servo_close_fuel()
            shutoff_time = time.ticks_ms()
            apogee_reached = True
            state = "coast_freefall"
            break

        if time.ticks_diff(time.ticks_ms(), burn_start) > SAFETY_TIMEOUT_MS:
            print("Safety timeout - shutting off")
            servo_close_fuel()
            state = "aborted_timeout"
            return

        time.sleep_ms(30)

    print("Monitoring for reapply window ({}-{} ft => {:.3f}-{:.3f} m)".format(
        REAPPLY_ALT_LOW_FT, REAPPLY_ALT_HIGH_FT, REAPPLY_ALT_LOW_M, REAPPLY_ALT_HIGH_M))
    reapply_done = False
    start_coast = time.ticks_ms()
    while True:
        ax,ay,az,gx,gy,gz = read_mpu6050()
        tempC, pressure = read_bmp280()
        d0, d1 = read_lidars()
        alt_m = None
        if d0 is not None and d1 is not None:
            alt_m = min(d0,d1)
        elif d0 is not None:
            alt_m = d0
        elif d1 is not None:
            alt_m = d1

        log_row(state, ax,ay,az,gx,gy,gz, tempC, pressure, d0, d1)

        if alt_m is not None and REAPPLY_ALT_LOW_M <= alt_m <= REAPPLY_ALT_HIGH_M:
            print("Reapply window hit (alt {:.2f} m). Pulsing thruster.".format(alt_m))

            servo_open_fuel()
            time.sleep_ms(30)
            try:
                igniter_power.value(1)
            except:
                pass
            servo_ignite_press()
            time.sleep_ms(IGNITE_PULSE_MS)
            servo_ignite_release()
            try:
                igniter_power.value(0)
            except:
                pass

            servo_close_fuel()

            print("Bounce pulse done. Deploying legs.")
            deploy_legs()
            reapply_done = True
            state = "post_bounce"
            break

        if time.ticks_diff(time.ticks_ms(), start_coast) > 120000:
            print("Coast timeout - abort")
            break

        time.sleep_ms(40)

    print("Mission sequence complete. Disarming servos.")

    for s in other_servos:
        s.detach()
    fuel_servo.detach()
    igniter_servo.detach()

if __name__ == "__main__":
    try:
        mission_main_loop()
    except Exception as e:
        print("Fatal error in mission:", e)

        try:
            servo_close_fuel()
            servo_ignite_release()
        except:
            pass

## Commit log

2025-07-15 added a body tube to simulate the leg ring
2025-07-20 set up the motor config for simulations
2025-07-21 ran a few simulations and everything looks fine for now
    can proceed with the cad model
2025-07-31 added CAD
    [ASTRA.stl]
2025-07-31 added schematics file
    [ASTRA.kicad_sch]
2025-07-31 added pcb
    [ASTRA.kicad_pcb]
2025-07-31 added bom and readme
    [BOM.csv]
2025-07-31 added images of the cad
2025-08-07 the current pcb files
    [ASTRA (1).kicad_sch, ASTRA (3).kicad_pcb, ASTRA.kicad_pcb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]
2025-08-21 the new pcb
    [ASTRA.kicad_pcb, ASTRA.kicad_sch]
2025-09-01 added the proper .step and .f3d files
    [astra.f3d, astra.step]
2025-09-06 added new pcb
    [ASTRA.kicad_pcb, ASTRA.kicad_sch]
2025-09-07 removed old files from tracking
    [ASTRA (1).kicad_sch, ASTRA (3).kicad_pcb, ASTRA.kicad_pcb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]
2025-09-07 a lil tweak on the pcb
    [ASTRA.kicad_pcb, ASTRA.kicad_sch]
2025-09-07 updated bom
    [BOM.csv]
2025-09-08 fixed the issue in the bom in readme and the csv
    [BOM.csv]
2025-09-08 fixed an issue with the bom at both the places
    [BOM.csv]
2025-09-11 new improved pcb
    [ASTRA.kicad_pcb, ASTRA.kicad_sch]
2025-09-11 deleted previous pcb files
    [ASTRA.kicad_pcb, ASTRA.kicad_sch]
2025-09-11 lil tweaks
    [ASTRA.kicad_pcb, ASTRA.kicad_sch]
2025-09-12 removed previous files
    [ASTRA.kicad_pcb, ASTRA.kicad_sch]
2025-09-13 added pcb image to the readme
2026-01-16 added new flight controller pcb files
    [ASTRA.kicad_pcb, ASTRA.kicad_sch]
